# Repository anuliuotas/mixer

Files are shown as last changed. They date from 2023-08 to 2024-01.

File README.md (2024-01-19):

TODO:

### KiCad:
- MixerController: Bad mosfet footprint G and D pins are mixed up
- All: Mounting holes should be grounded
- All: Pinout should be visible at least in drawings layer

### ESPHome
- MixerController: VESC temperature sensor reading from CAN
- MixerInterface: Loading splash screen

### CAD
- Increase height of WAGO holder for more cable space

### Other
- Buy standoffs for VESC cover holder
- Check replacement parts

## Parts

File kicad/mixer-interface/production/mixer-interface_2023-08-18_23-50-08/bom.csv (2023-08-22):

Designator | Footprint | Quantity | Value | LCSC Part #
C1 | 0805 | 1 | 10u
H1, H2, H3, H4 | MountingHole_3.2mm_M3_Pad_Via | 4 | MountingHole
J1 | JST_XH_B2B-XH-AM_1x02_P2.50mm_Vertical | 1 | PWR_IN
J2 | JST_XH_B2B-XH-AM_1x02_P2.50mm_Vertical | 1 | CAN
R1, R2 | 0805 | 2 | 10k
R3, R4, R6 | 0805 | 3 | 4k7
R5 | 0805 | 1 | R120
U10 | MODULE_ESP32-DEVKITC-32U | 1 | ESP32-DEVKITC-32U
U2 | JST_XH_B5B-XH-AM_1x05_P2.50mm_Vertical | 1 | TIME_ENCODER
U3 | JST_XH_B5B-XH-AM_1x05_P2.50mm_Vertical | 1 | SPEED_ENCODER
U4 | JST_XH_B3B-XH-AM_1x03_P2.50mm_Vertical | 1 | TEMP MOTOR
U5 | JST_XH_B3B-XH-AM_1x03_P2.50mm_Vertical | 1 | TEMP MATERIAL
U6 | TJA1050 | 1 | TJA1050
U8 | display_connector_jst_xh_6 | 1 | TZT OLED312 SSD1322

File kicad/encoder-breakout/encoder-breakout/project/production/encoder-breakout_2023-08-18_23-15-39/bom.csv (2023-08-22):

Designator | Footprint | Quantity | Value | LCSC Part #
C1, C2, C3 | 0805 | 3 | C
J1 | JST_XH_S5B-XH-A_1x05_P2.50mm_Horizontal | 1 | Conn_01x05_Socket
R3, R4, R5 | 0805 | 3 | 10k
SW1 | RotaryEncoder_Alps_EC11E-Switch_Vertical_H20mm | 1 | RotaryEncoder_Switch

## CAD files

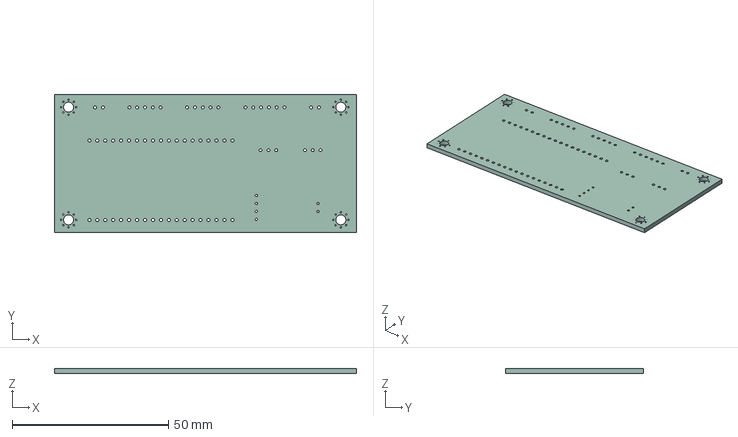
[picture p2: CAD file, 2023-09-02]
kicad/mixer-interface/mixer-interface.step
96.5 x 44.0 x 1.58 mm

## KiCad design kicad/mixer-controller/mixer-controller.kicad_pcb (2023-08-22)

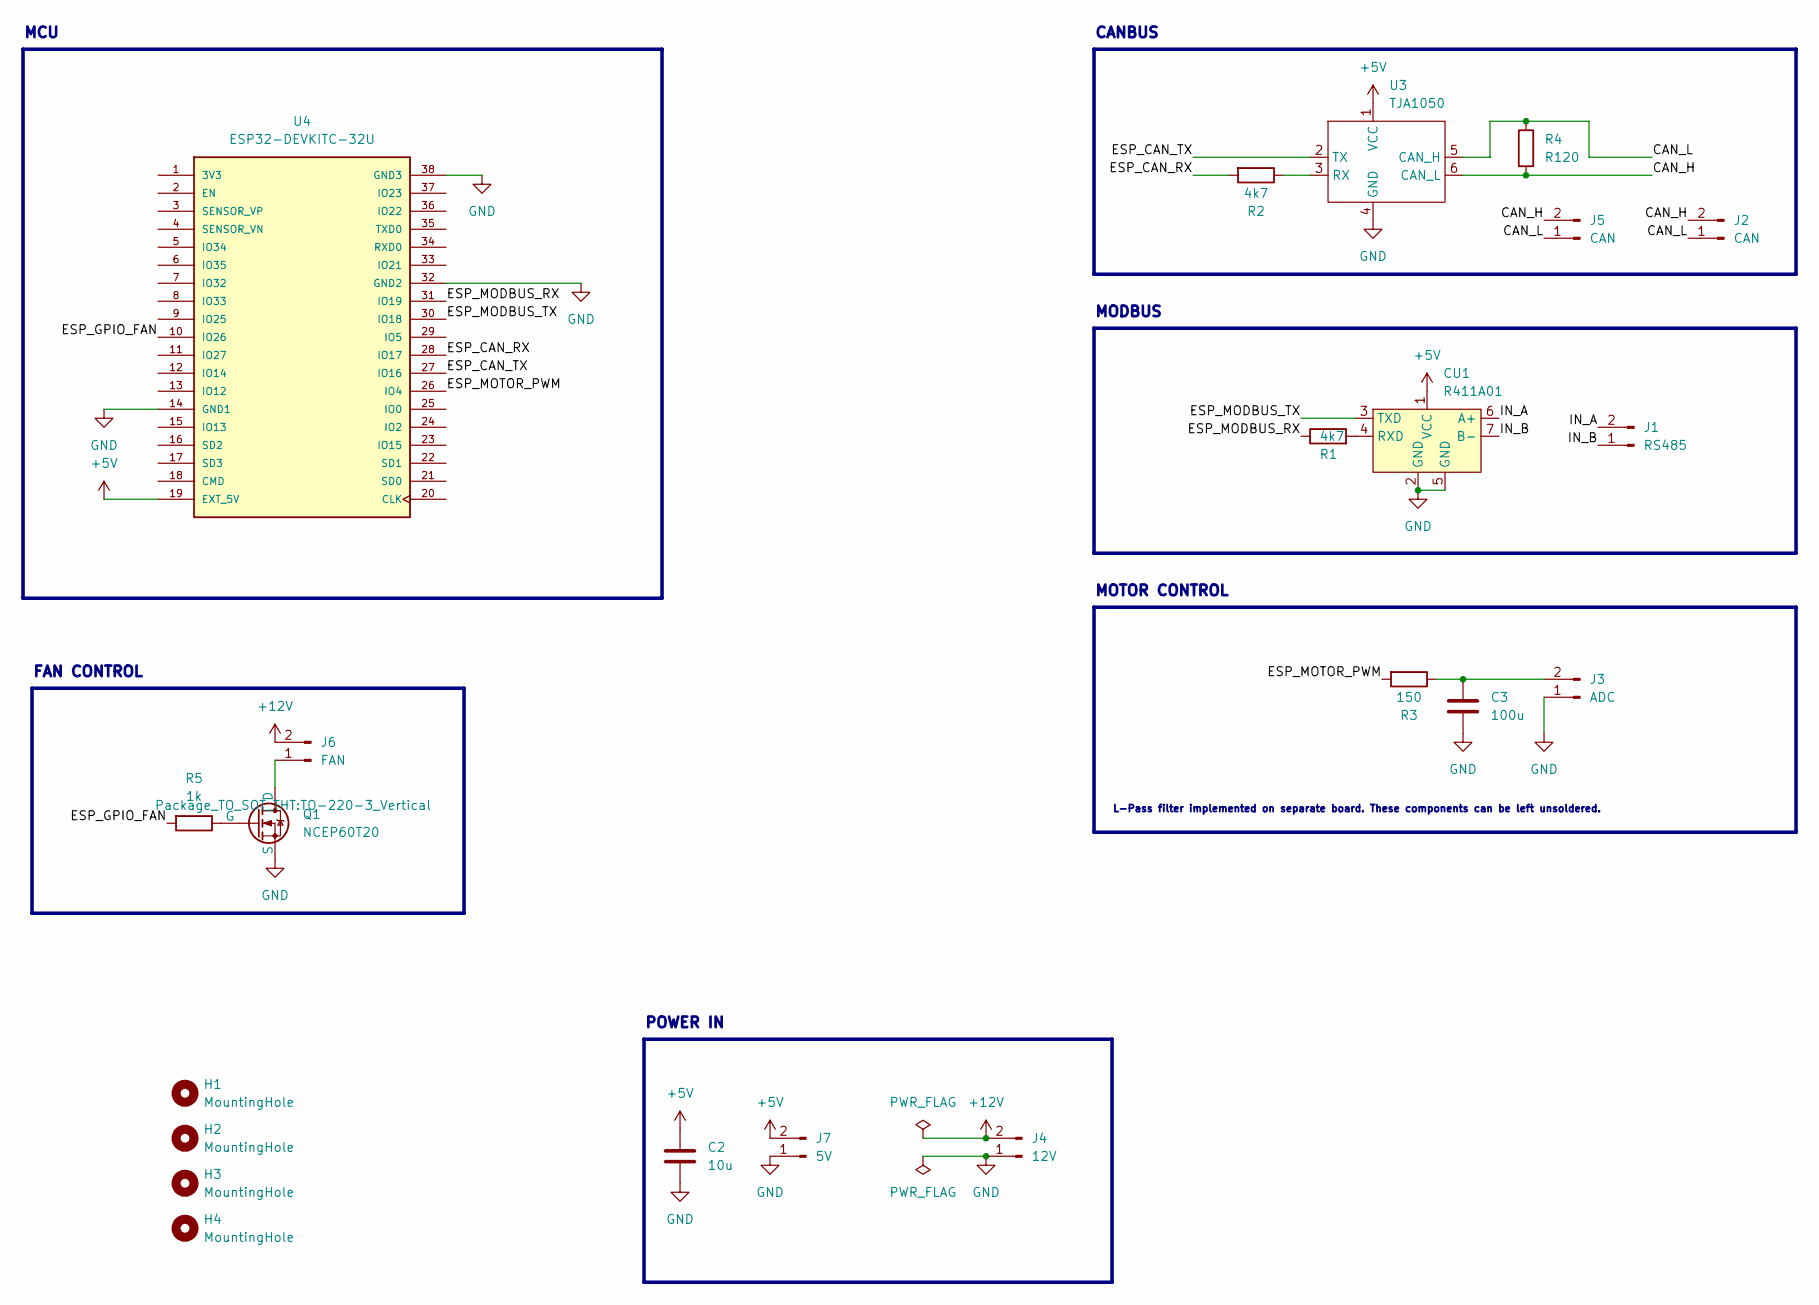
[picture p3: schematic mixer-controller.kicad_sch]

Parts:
C2: 10u; C_0805_2012Metric
C3: 100u; C_0805_2012Metric
CU1: R411A01
H1, H2, H3, H4: MountingHole; MountingHole_3.2mm_M3_Pad_Via
J1: RS485; JST_XH_B2B-XH-A_1x02_P2.50mm_Vertical
J2, J5: CAN; JST_XH_B2B-XH-A_1x02_P2.50mm_Vertical
J3: ADC; JST_XH_B2B-XH-A_1x02_P2.50mm_Vertical
J4: 12V; JST_XH_B2B-XH-A_1x02_P2.50mm_Vertical
J6: FAN; JST_XH_B2B-XH-A_1x02_P2.50mm_Vertical
J7: 5V; JST_XH_B2B-XH-A_1x02_P2.50mm_Vertical
Q1: NCEP60T20; TO-220-3_Vertical
R1: 4k7; R_0805_2012Metric
R2: 4k7; R_0805_2012Metric_Pad1.20x1.40mm_HandSolder
R3: 150; R_0805_2012Metric_Pad1.20x1.40mm_HandSolder
R4: R120; R_0805_2012Metric_Pad1.20x1.40mm_HandSolder
R5: 1k; R_0805_2012Metric_Pad1.20x1.40mm_HandSolder
U3: TJA1050
U4: ESP32-DEVKITC-32U; MODULE_ESP32-DEVKITC-32U; PARTREV N/A

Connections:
+5V: C2.1, CU1.1 (VCC), J7.2, U3.1 (VCC), U4.19 (EXT_5V)
+12V: J4.2, J6.2
/CAN_H: J2.2, J5.2, R4.2, U3.6 (CAN_L)
/CAN_L: J2.1, J5.1, R4.1, U3.5 (CAN_H)
/ESP_CAN_RX: R2.2, U4.28 (IO17)
/ESP_CAN_TX: U3.2 (TX), U4.27 (IO16)
/ESP_GPIO_FAN: R5.2, U4.10 (IO26)
/ESP_MODBUS_RX: R1.1, U4.31 (IO19)
/ESP_MODBUS_TX: CU1.3 (TXD), U4.30 (IO18)
/ESP_MOTOR_PWM: R3.2, U4.26 (IO4)
/IN_A: CU1.6 (A+), J1.2
/IN_B: CU1.7 (B-), J1.1
GND: C2.2, C3.2, CU1.2 (GND), CU1.5 (GND), J3.1, J4.1, J7.1, Q1.3 (S), U3.4 (GND), U4.14 (GND1), U4.32 (GND2), U4.38 (GND3)
unnamed: CU1.4 (RXD), R1.2
unnamed: C3.1, J3.2, R3.1
unnamed: J6.1, Q1.1 (D)
unnamed: Q1.2 (G), R5.1
unnamed: R2.1, U3.3 (RX)

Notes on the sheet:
POWER IN
FAN CONTROL
MODBUS
MCU
MOTOR CONTROL
L-Pass filter implemented on separate board. These components can be left unsoldered.
CANBUS

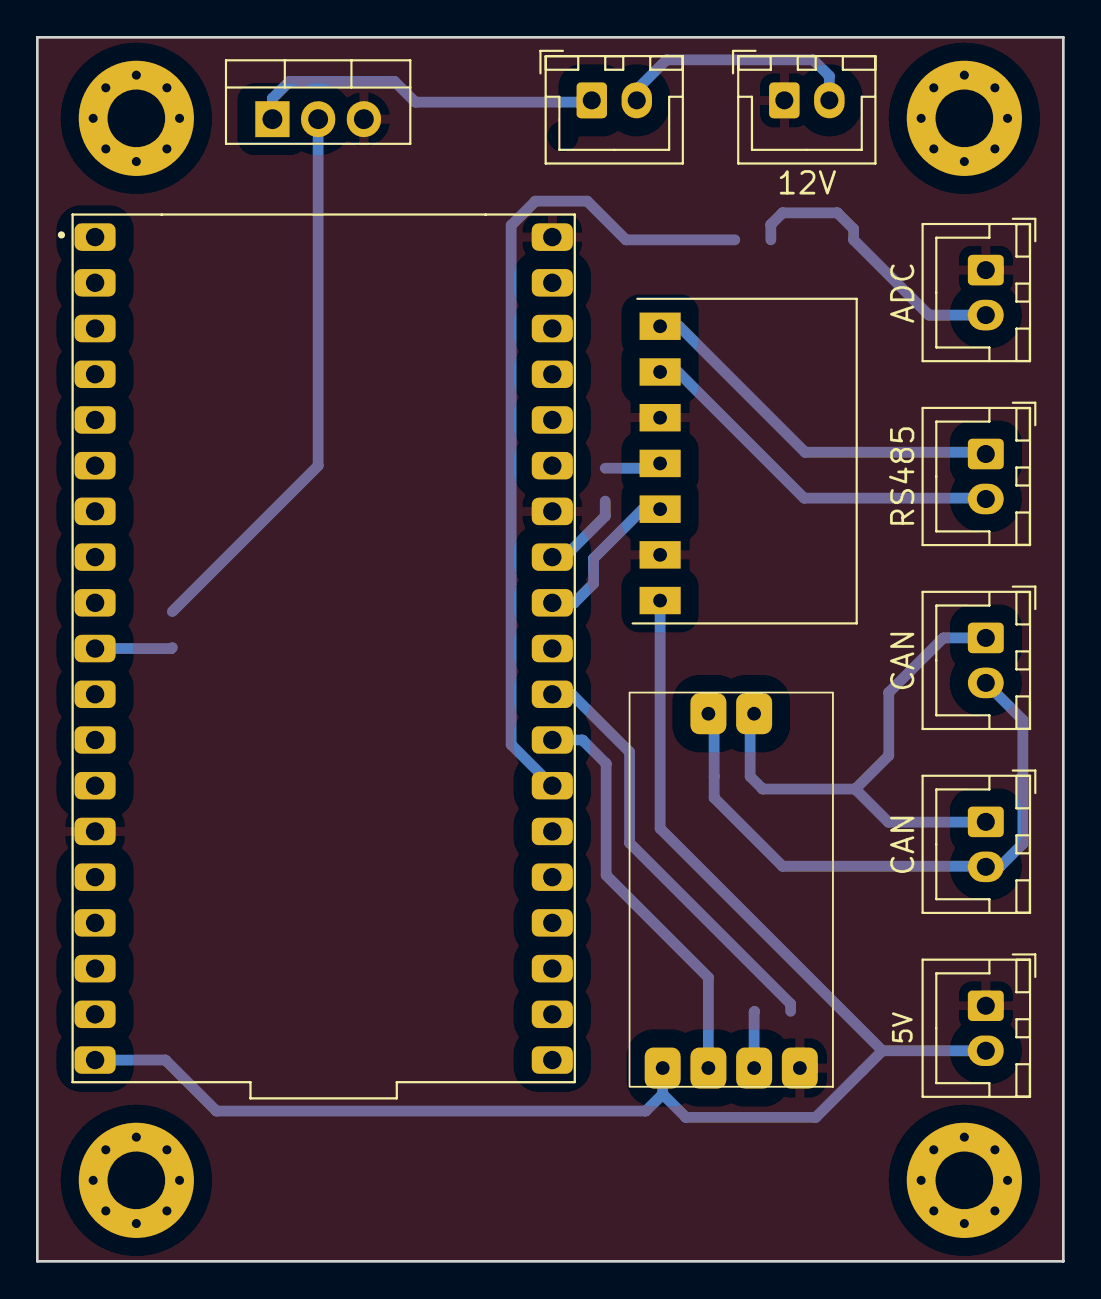
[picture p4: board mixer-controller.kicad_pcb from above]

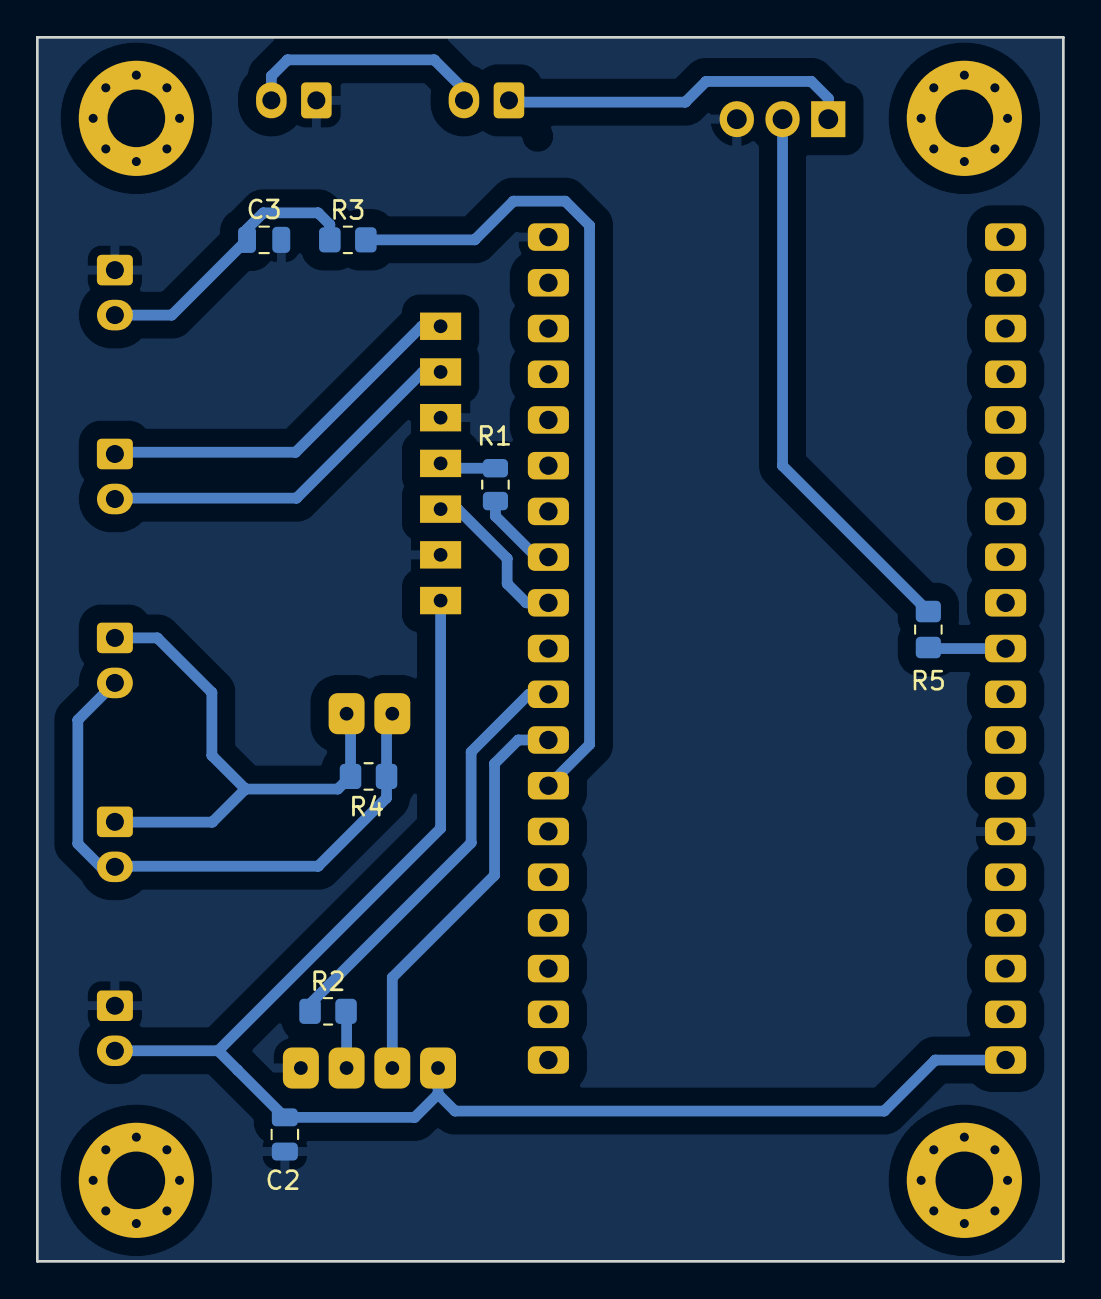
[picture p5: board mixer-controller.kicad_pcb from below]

Board: 2 copper layers, 57.0 x 68.0 mm, 22 parts (7 on the bottom side), 18 nets.

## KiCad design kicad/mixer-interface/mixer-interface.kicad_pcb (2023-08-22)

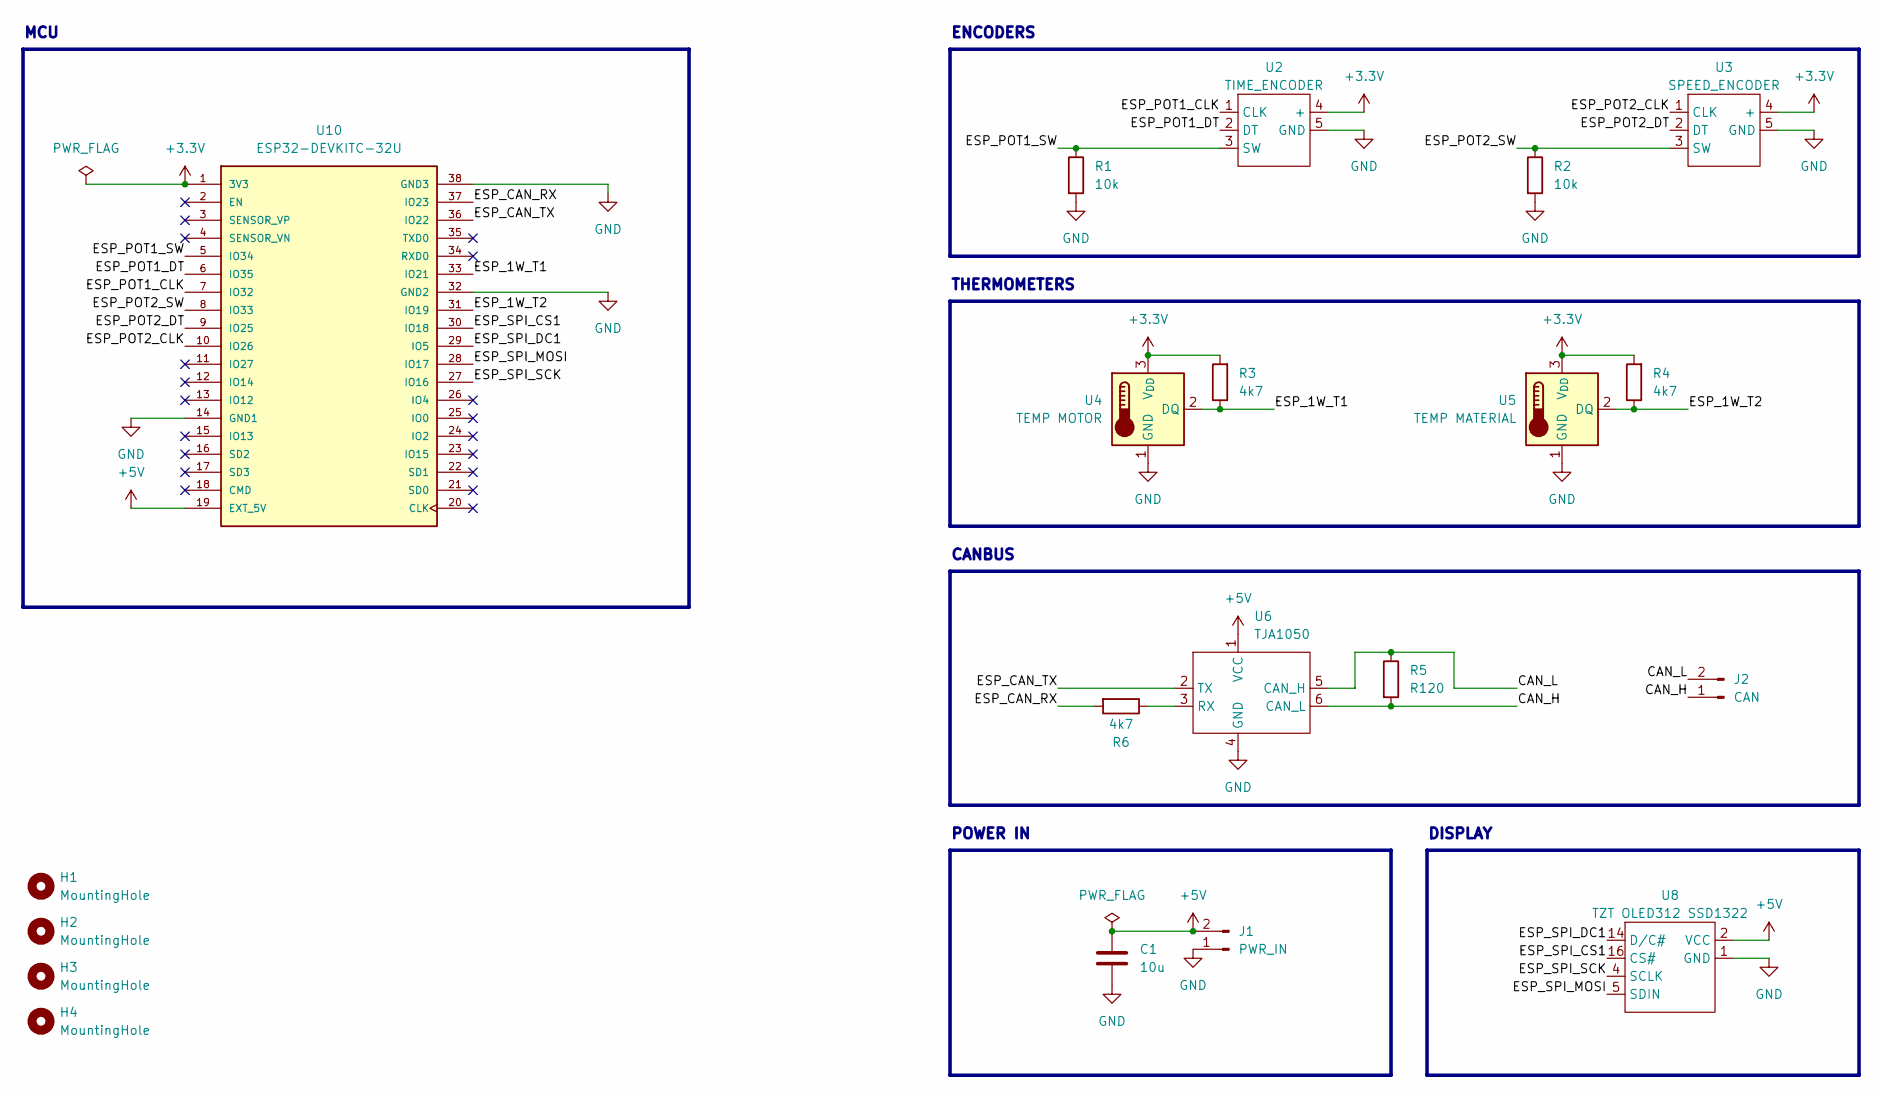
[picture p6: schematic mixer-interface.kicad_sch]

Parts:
C1: 10u; C_0805_2012Metric
H1, H2, H3, H4: MountingHole; MountingHole_3.2mm_M3_Pad_Via
J1: PWR_IN; JST_XH_B2B-XH-A_1x02_P2.50mm_Vertical
J2: CAN; JST_XH_B2B-XH-A_1x02_P2.50mm_Vertical
R1, R2: 10k; R_0805_2012Metric_Pad1.20x1.40mm_HandSolder
R3, R4, R6: 4k7; R_0805_2012Metric_Pad1.20x1.40mm_HandSolder
R5: R120; R_0805_2012Metric_Pad1.20x1.40mm_HandSolder
U2: TIME_ENCODER; JST_XH_B5B-XH-A_1x05_P2.50mm_Vertical
U3: SPEED_ENCODER; JST_XH_B5B-XH-A_1x05_P2.50mm_Vertical
U4: TEMP MOTOR; JST_XH_B3B-XH-A_1x03_P2.50mm_Vertical
U5: TEMP MATERIAL; JST_XH_B3B-XH-A_1x03_P2.50mm_Vertical
U6: TJA1050
U8: TZT OLED312 SSD1322; display_connector_jst_xh_6
U10: ESP32-DEVKITC-32U; MODULE_ESP32-DEVKITC-32U; PARTREV N/A

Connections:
+3.3V: R3.2, R4.2, U2.4 (+), U3.4 (+), U4.3 (V_{DD}), U5.3 (V_{DD}), U10.1 (3V3)
+5V: C1.1, J1.2, U6.1 (VCC), U8.2 (VCC), U10.19 (EXT_5V)
/CAN_H: J2.1, R5.2, U6.6 (CAN_L)
/CAN_L: J2.2, R5.1, U6.5 (CAN_H)
/ESP_1W_T1: R3.1, U4.2 (DQ), U10.33 (IO21)
/ESP_1W_T2: R4.1, U5.2 (DQ), U10.31 (IO19)
/ESP_CAN_RX: R6.2, U10.37 (IO23)
/ESP_CAN_TX: U6.2 (TX), U10.36 (IO22)
/ESP_POT1_CLK: U2.1 (CLK), U10.7 (IO32)
/ESP_POT1_DT: U2.2 (DT), U10.6 (IO35)
/ESP_POT1_SW: R1.1, U2.3 (SW), U10.5 (IO34)
/ESP_POT2_CLK: U3.1 (CLK), U10.10 (IO26)
/ESP_POT2_DT: U3.2 (DT), U10.9 (IO25)
/ESP_POT2_SW: R2.1, U3.3 (SW), U10.8 (IO33)
/ESP_SPI_CS1: U8.16 (CS#), U10.30 (IO18)
/ESP_SPI_DC1: U8.14 (D/C#), U10.29 (IO5)
/ESP_SPI_MOSI: U8.5 (SDIN), U10.28 (IO17)
/ESP_SPI_SCK: U8.4 (SCLK), U10.27 (IO16)
GND: C1.2, J1.1, R1.2, R2.2, U2.5 (GND), U3.5 (GND), U4.1 (GND), U5.1 (GND), U6.4 (GND), U8.1 (GND), U10.14 (GND1), U10.32 (GND2), U10.38 (GND3)
unnamed: R6.1, U6.3 (RX)

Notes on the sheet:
CANBUS
DISPLAY
MCU
POWER IN
THERMOMETERS
ENCODERS

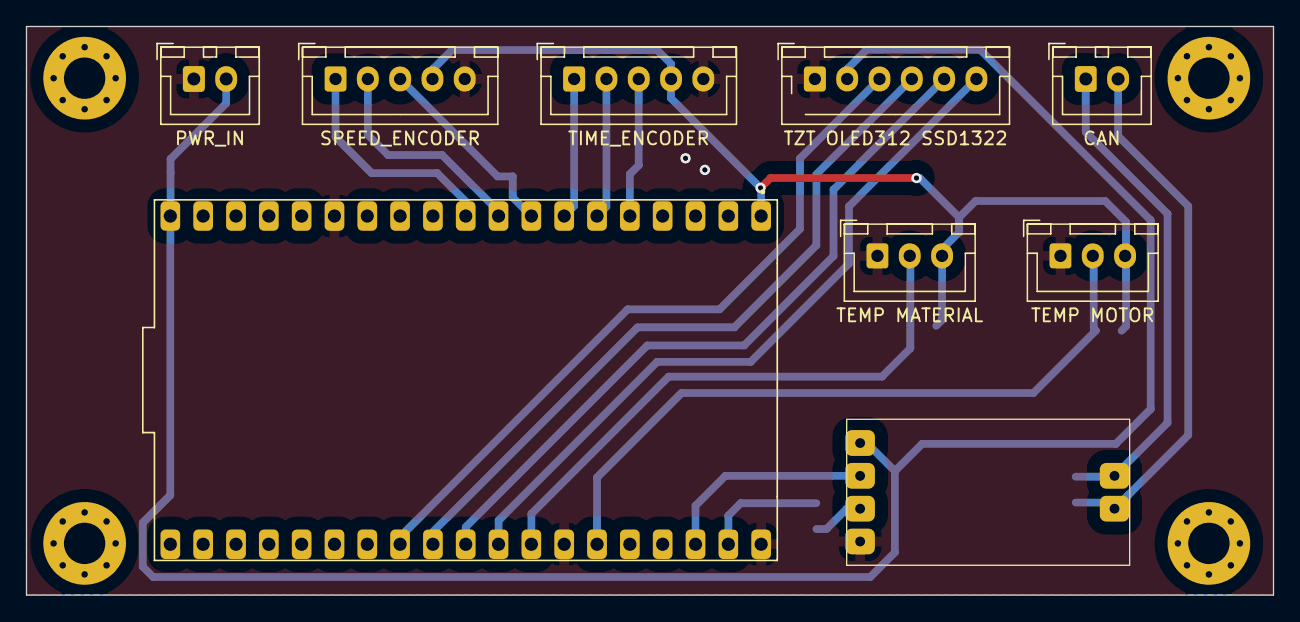
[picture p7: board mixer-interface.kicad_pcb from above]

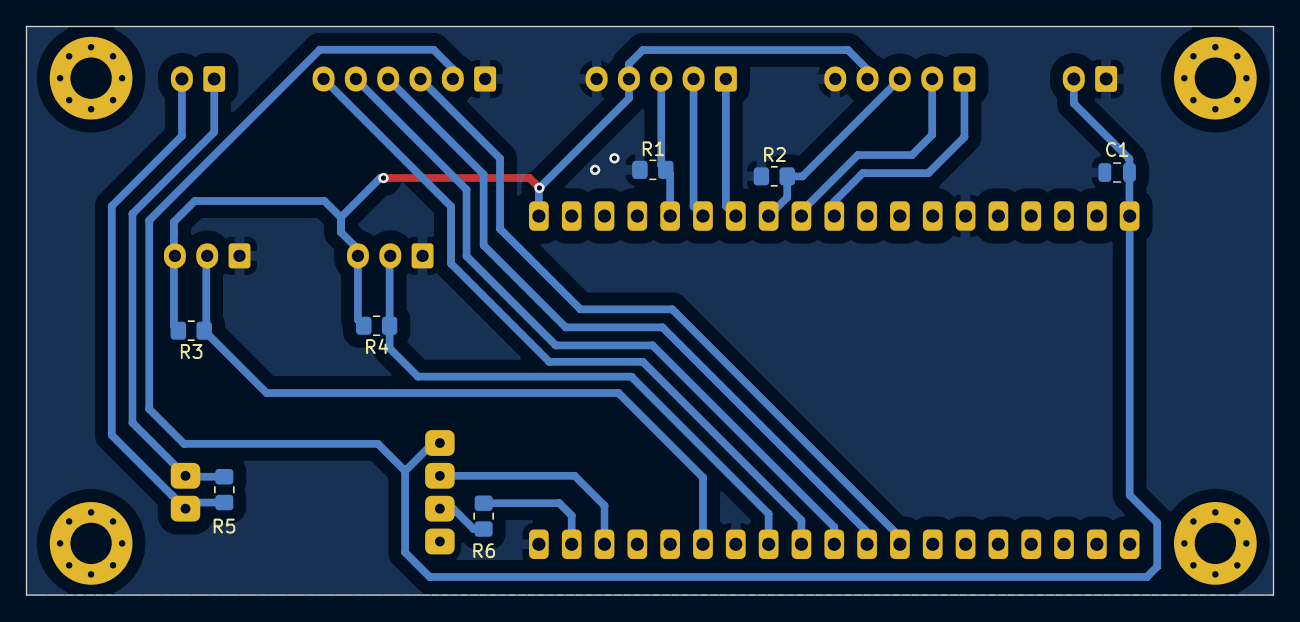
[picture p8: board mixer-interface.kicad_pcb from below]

Board: 2 copper layers, 96.5 x 44.0 mm, 20 parts (7 on the bottom side), 20 nets.

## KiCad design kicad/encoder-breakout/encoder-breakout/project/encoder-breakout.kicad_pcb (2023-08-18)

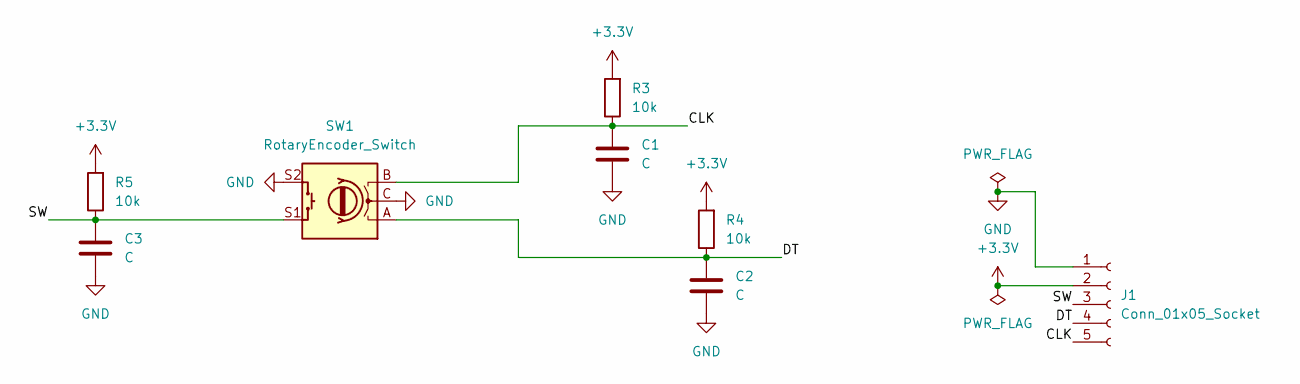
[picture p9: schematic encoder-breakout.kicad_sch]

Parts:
C1, C2, C3: C; C_0805_2012Metric_Pad1.18x1.45mm_HandSolder
J1: Conn_01x05_Socket; JST_XH_S5B-XH-A_1x05_P2.50mm_Horizontal
R3, R4, R5: 10k; R_0805_2012Metric_Pad1.20x1.40mm_HandSolder
SW1: RotaryEncoder_Switch; RotaryEncoder_Alps_EC11E-Switch_Vertical_H20mm

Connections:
+3.3V: J1.2, R3.2, R4.2, R5.2
/CLK: C1.1, J1.5, R3.1, SW1.B
/DT: C2.1, J1.4, R4.1, SW1.A
/SW: C3.1, J1.3, R5.1, SW1.S1
GND: C1.2, C2.2, C3.2, J1.1, SW1.C, SW1.S2

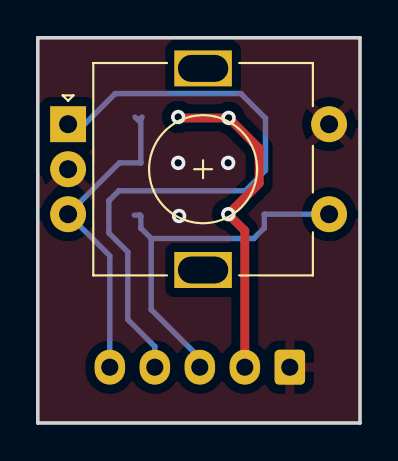
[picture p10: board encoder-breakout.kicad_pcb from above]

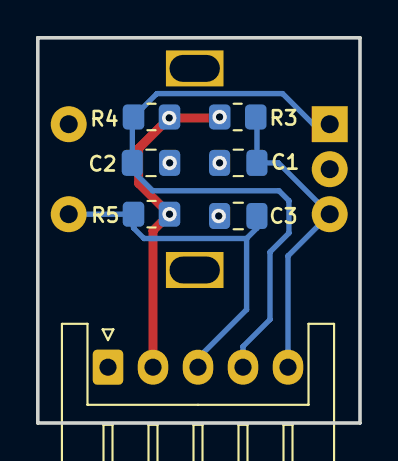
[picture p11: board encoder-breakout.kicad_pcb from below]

Board: 2 copper layers, 17.9 x 21.4 mm, 8 parts (7 on the bottom side), 5 nets.

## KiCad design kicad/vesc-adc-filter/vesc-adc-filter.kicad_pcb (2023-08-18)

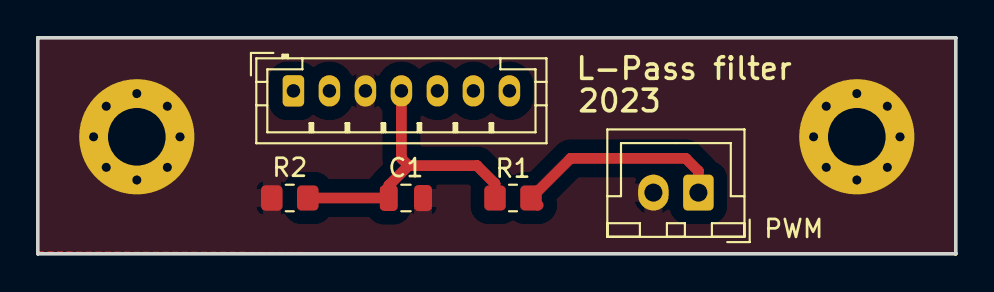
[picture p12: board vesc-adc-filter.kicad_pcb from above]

Board: 2 copper layers, 51.0 x 12.0 mm, 7 parts (0 on the bottom side), 3 nets.

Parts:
C1: 100u; C_0805_2012Metric
H1, H2: MountingHole; MountingHole_3.2mm_M3_Pad_Via
J1: PWM; JST_XH_B2B-XH-A_1x02_P2.50mm_Vertical
R1: 150; R_0805_2012Metric_Pad1.20x1.40mm_HandSolder
R2: 100k; R_0805_2012Metric_Pad1.20x1.40mm_HandSolder
U1: JST_PH_B7B-PH-K_1x07_P2.00mm_Vertical

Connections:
GND: C1.2, J1.2, R2.2, U1.3 (GND)
unnamed: J1.1, R1.2
unnamed: C1.1, R1.1, R2.1, U1.4 (ADC1)

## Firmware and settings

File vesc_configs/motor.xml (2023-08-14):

<?xml version="1.0" encoding="UTF-8"?>
<MCConfiguration>
    <pwm_mode>1</pwm_mode>
    <comm_mode>0</comm_mode>
    <motor_type>2</motor_type>
    <sensor_mode>0</sensor_mode>
    <l_current_max>15</l_current_max>
    <l_current_min>0</l_current_min>
    <l_in_current_max>15</l_in_current_max>
    <l_in_current_min>0</l_in_current_min>
    <l_abs_current_max>18</l_abs_current_max>
    <l_min_erpm>-100000</l_min_erpm>
    <l_max_erpm>100000</l_max_erpm>
    <l_erpm_start>0.8</l_erpm_start>
    <l_max_erpm_fbrake>300</l_max_erpm_fbrake>
    <l_max_erpm_fbrake_cc>1500</l_max_erpm_fbrake_cc>
    <l_min_vin>8</l_min_vin>
    <l_max_vin>57</l_max_vin>
    <l_battery_cut_start>10</l_battery_cut_start>
    <l_battery_cut_end>8</l_battery_cut_end>
    <l_slow_abs_current>1</l_slow_abs_current>
    <l_temp_fet_start>60</l_temp_fet_start>
    <l_temp_fet_end>70</l_temp_fet_end>
    <l_temp_motor_start>85</l_temp_motor_start>
    <l_temp_motor_end>100</l_temp_motor_end>
    <l_temp_accel_dec>0.15</l_temp_accel_dec>
    <l_min_duty>0</l_min_duty>
    <l_max_duty>0.95</l_max_duty>
    <l_watt_max>1.5e+06</l_watt_max>
    <l_watt_min>-1.5e+06</l_watt_min>
    <l_current_max_scale>1</l_current_max_scale>
    <l_current_min_scale>1</l_current_min_scale>
    <l_duty_start>1</l_duty_start>
    <sl_min_erpm>150</sl_min_erpm>
    <sl_min_erpm_cycle_int_limit>1100</sl_min_erpm_cycle_int_limit>
    <sl_max_fullbreak_current_dir_change>10</sl_max_fullbreak_current_dir_change>
    <sl_cycle_int_limit>62</sl_cycle_int_limit>
    <sl_phase_advance_at_br>0.8</sl_phase_advance_at_br>
    <sl_cycle_int_rpm_br>80000</sl_cycle_int_rpm_br>
    <sl_bemf_coupling_k>600</sl_bemf_coupling_k>
    <hall_table__0>-1</hall_table__0>
    <hall_table__1>1</hall_table__1>
    <hall_table__2>3</hall_table__2>
    <hall_table__3>2</hall_table__3>
    <hall_table__4>5</hall_table__4>
    <hall_table__5>6</hall_table__5>
    <hall_table__6>4</hall_table__6>
    <hall_table__7>-1</hall_table__7>
    <hall_sl_erpm>2000</hall_sl_erpm>
    <foc_current_kp>0.0044</foc_current_kp>
    <foc_current_ki>33.17</foc_current_ki>
    <foc_f_sw>40000</foc_f_sw>
    <foc_dt_us>0.12</foc_dt_us>
    <foc_encoder_inverted>0</foc_encoder_inverted>
    <foc_encoder_offset>180</foc_encoder_offset>
    <foc_encoder_ratio>7</foc_encoder_ratio>
    <foc_encoder_sin_gain>1</foc_encoder_sin_gain>
    <foc_encoder_cos_gain>1</foc_encoder_cos_gain>
    <foc_encoder_sin_offset>1.65</foc_encoder_sin_offset>
    <foc_encoder_cos_offset>1.65</foc_encoder_cos_offset>
    <foc_encoder_sincos_filter_constant>0.5</foc_encoder_sincos_filter_constant>
    <foc_sensor_mode>0</foc_sensor_mode>
    <foc_pll_kp>2000</foc_pll_kp>
    <foc_pll_ki>30000</foc_pll_ki>
    <foc_motor_l>4.45e-06</foc_motor_l>
    <foc_motor_r>0.0332</foc_motor_r>
    <foc_motor_flux_linkage>0.002464</foc_motor_flux_linkage>
    <foc_observer_gain>1.6471e+08</foc_observer_gain>
    <foc_observer_gain_slow>0.05</foc_observer_gain_slow>
    <foc_duty_dowmramp_kp>10</foc_duty_dowmramp_kp>
    <foc_duty_dowmramp_ki>200</foc_duty_dowmramp_ki>
    <foc_openloop_rpm>400</foc_openloop_rpm>
    <foc_sl_openloop_hyst>0.1</foc_sl_openloop_hyst>
    <foc_sl_openloop_time>0.1</foc_sl_openloop_time>
    <foc_sl_d_current_duty>0</foc_sl_d_current_duty>
    <foc_sl_d_current_factor>0</foc_sl_d_current_factor>
    <foc_hall_table__0>255</foc_hall_table__0>
    <foc_hall_table__1>255</foc_hall_table__1>
    <foc_hall_table__2>255</foc_hall_table__2>
    <foc_hall_table__3>255</foc_hall_table__3>
    <foc_hall_table__4>255</foc_hall_table__4>
    <foc_hall_table__5>255</foc_hall_table__5>
    <foc_hall_table__6>255</foc_hall_table__6>
    <foc_hall_table__7>255</foc_hall_table__7>
    <foc_sl_erpm>2500</foc_sl_erpm>
    <foc_sample_v0_v7>0</foc_sample_v0_v7>
    <foc_sample_high_current>0</foc_sample_high_current>
    <foc_sat_comp>0</foc_sat_comp>
    <foc_temp_comp>0</foc_temp_comp>
    <foc_temp_comp_base_temp>25</foc_temp_comp_base_temp>
    <foc_current_filter_const>0.1</foc_current_filter_const>
    <foc_cc_decoupling>2</foc_cc_decoupling>
    <foc_observer_type>0</foc_observer_type>
    <foc_hfi_voltage_start>20</foc_hfi_voltage_start>
    <foc_hfi_voltage_run>4</foc_hfi_voltage_run>
    <foc_hfi_voltage_max>10</foc_hfi_voltage_max>
    <foc_sl_erpm_hfi>2000</foc_sl_erpm_hfi>
    <foc_hfi_start_samples>65</foc_hfi_start_samples>
    <foc_hfi_obs_ovr_sec>0.001</foc_hfi_obs_ovr_sec>
    <foc_hfi_samples>1</foc_hfi_samples>
    <gpd_buffer_notify_left>200</gpd_buffer_notify_left>
    <gpd_buffer_interpol>0</gpd_buffer_interpol>
    <gpd_current_filter_const>0.1</gpd_current_filter_const>
    <gpd_current_kp>0.03</gpd_current_kp>
    <gpd_current_ki>50</gpd_current_ki>
    <s_pid_kp>0.004</s_pid_kp>
    <s_pid_ki>0.004</s_pid_ki>
    <s_pid_kd>0.0001</s_pid_kd>
    <s_pid_kd_filter>0.2</s_pid_kd_filter>
    <s_pid_min_erpm>900</s_pid_min_erpm>
    <s_pid_allow_braking>1</s_pid_allow_braking>
    <p_pid_kp>0.03</p_pid_kp>
    <p_pid_ki>0</p_pid_ki>
    <p_pid_kd>0.0004</p_pid_kd>
    <p_pid_kd_filter>0.2</p_pid_kd_filter>
    <p_pid_ang_div>1</p_pid_ang_div>
    <cc_startup_boost_duty>0.01</cc_startup_boost_duty>
    <cc_min_current>0.05</cc_min_current>
    <cc_gain>0.0046</cc_gain>
    <cc_ramp_step_max>0.04</cc_ramp_step_max>
    <m_fault_stop_time_ms>500</m_fault_stop_time_ms>
    <m_duty_ramp_step>0.02</m_duty_ramp_step>
    <m_current_backoff_gain>0.5</m_current_backoff_gain>
    <m_encoder_counts>8192</m_encoder_counts>
    <m_sensor_port_mode>0</m_sensor_port_mode>
    <m_invert_direction>1</m_invert_direction>
    <m_drv8301_oc_mode>3</m_drv8301_oc_mode>
    <m_drv8301_oc_adj>25</m_drv8301_oc_adj>
    <m_bldc_f_sw_min>3000</m_bldc_f_sw_min>
    <m_bldc_f_sw_max>35000</m_bldc_f_sw_max>
    <m_dc_f_sw>25000</m_dc_f_sw>
    <m_ntc_motor_beta>3380</m_ntc_motor_beta>
    <m_out_aux_mode>0</m_out_aux_mode>
    <m_motor_temp_sens_type>0</m_motor_temp_sens_type>
    <m_ptc_motor_coeff>0.61</m_ptc_motor_coeff>
    <si_motor_poles>14</si_motor_poles>
    <si_gear_ratio>3</si_gear_ratio>
    <si_wheel_diameter>0.083</si_wheel_diameter>
    <si_battery_type>0</si_battery_type>
    <si_battery_cells>3</si_battery_cells>
    <si_battery_ah>6</si_battery_ah>
    <motor_brand>Unnamed</motor_brand>
    <motor_model>Not Specified</motor_model>
    <motor_weight>0</motor_weight>
    <motor_poles>14</motor_poles>
    <motor_sensor_type>0</motor_sensor_type>
    <motor_description>&lt;!DOCTYPE HTML PUBLIC &quot;-//W3C//DTD HTML 4.0//EN&quot; &quot;http://www.w3.org/TR/REC-html40/strict.dtd&quot;&gt;
&lt;html&gt;&lt;head&gt;&lt;meta name=&quot;qrichtext&quot; content=&quot;1&quot; /&gt;&lt;style type=&quot;text/css&quot;&gt;
p, li { white-space: pre-wrap; }
&lt;/style&gt;&lt;/head&gt;&lt;body style=&quot; font-family:'Roboto'; font-size:12pt; font-weight:400; font-style:normal;&quot;&gt;
&lt;p style=&quot; margin-top:0px; margin-bottom:0px; margin-left:0px; margin-right:0px; -qt-block-indent:0; text-indent:0px;&quot;&gt;A motor description can be edited here.&lt;/p&gt;&lt;/body&gt;&lt;/html&gt;</motor_description>
    <motor_loss_torque>0.03</motor_loss_torque>
    <motor_quality_bearings>0</motor_quality_bearings>
    <motor_quality_magnets>0</motor_quality_magnets>
    <motor_quality_construction>0</motor_quality_construction>
    <motor_quality_description>&lt;!DOCTYPE HTML PUBLIC &quot;-//W3C//DTD HTML 4.0//EN&quot; &quot;http://www.w3.org/TR/REC-html40/strict.dtd&quot;&gt;
&lt;html&gt;&lt;head&gt;&lt;meta name=&quot;qrichtext&quot; content=&quot;1&quot; /&gt;&lt;style type=&quot;text/css&quot;&gt;
p, li { white-space: pre-wrap; }
&lt;/style&gt;&lt;/head&gt;&lt;body style=&quot; font-family:'Roboto'; font-size:12pt; font-weight:400; font-style:normal;&quot;&gt;
&lt;p style=&quot; margin-top:0px; margin-bottom:0px; margin-left:0px; margin-right:0px; -qt-block-indent:0; text-indent:0px;&quot;&gt;Some comments about the motor quality. Images can be added as well.&lt;/p&gt;&lt;/body&gt;&lt;/html&gt;</motor_quality_description>
</MCConfiguration>

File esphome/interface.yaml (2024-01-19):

substitutions:
  device_name: "mixer-test"
  device_friendly_name: "Mixer test"
  mqqt_root_topic: "device"
  mqqt_retain_message: "false"

esphome:
  name: ${device_name}
  friendly_name: ${device_friendly_name}

esp32:
  board: nodemcu-32s

logger:
  level: INFO
  baud_rate: 9600
  logs:
    canbus: INFO

dallas:
  - pin: GPIO19
    id: hub_1
    update_interval: 5s
  - pin: GPIO21
    id: hub_2
    update_interval: 5s

sensor:
  - platform: dallas
    dallas_id: hub_1
    id: temp_motor
    index: 0

  - platform: dallas
    dallas_id: hub_2
    id: temp_material
    index: 0

  - platform: rotary_encoder
    id: time_encoder
    name: "Time encoder"
    pin_a: GPIO25
    pin_b: GPIO26
    min_value: 0
    max_value: 6000
    restore_mode: ALWAYS_ZERO
    resolution: 2
    filters:
      - multiply: 5
      - lambda: |-
          // If timer is ON, encoder value change is not allowed
          if (id(timer_state).state) {
            return {};
          }
          return x;
  
  - platform: rotary_encoder
    id: speed_encoder
    name: "Speed encoder"
    pin_a: GPIO35
    pin_b: GPIO32
    min_value: 0
    max_value: 100
    restore_mode: ALWAYS_ZERO
    resolution: 2
    filters:
      - multiply: 1

binary_sensor:
  - platform: gpio
    id: time_encoder_sw
    pin:
      number: GPIO33
      inverted: true
    on_press:
      then:
        - switch.toggle: timer_state
    
  - platform: gpio
    id: speed_encoder_sw
    pin:
      number: GPIO34
      inverted: true
    on_press:
      then:
        - switch.toggle: motor_state

switch:
  - platform: template
    id: motor_state
    optimistic: true
    restore_mode: ALWAYS_OFF
  - platform: template
    id: timer_state
    optimistic: true
    restore_mode: ALWAYS_OFF
    turn_on_action:
      - lambda: |-
          id(timer_update_ms) = 0;


globals:
  - id: timer_counter_ms
    type: long
    initial_value: '0'
    restore_value: no
  - id: timer_update_ms
    type: long
    initial_value: '0'
    restore_value: no
  - id: text_blink
    type: bool
    restore_value: no
  - id: speed_esp_rpm
    type: float
    initial_value: '0'
    restore_value: no

interval:
  # - interval: 250ms
  #   then:
  #       - lambda: |-
  #           // Text blink interval
  #           id(text_blink) = !id(text_blink);

  - interval: 100ms
    then:
      - lambda: |-
          // Udate timer
          if (id(timer_state).state) {
            
            // Update timer counter
            long current_millis = millis();
            long previous_timer_update_ms = id(timer_update_ms);

            if (previous_timer_update_ms == 0) {
              id(timer_update_ms) = current_millis;
              return;
            }

            long delta_millis = current_millis - previous_timer_update_ms;
            long updated_value = id(timer_counter_ms) + delta_millis;

            id(timer_counter_ms) = updated_value;
            id(timer_update_ms) = current_millis;

            if (float(updated_value) / 1000 > id(time_encoder).state) {
              // Timer has reach the setpoint
              id(timer_state).turn_off();
              id(motor_state).turn_off();

              id(timer_counter_ms) = 0;
              id(timer_update_ms) = 0;
            }
          } 
          
  - interval: 500ms
    then:
      - lambda: |-
          //if (millis() < 0) {
          //  return;
          //}
          // Send CAN bus message updating the speed setpoint

          int setpoint_req = 0;
          if (id(motor_state).state) {
            if (!isnan(id(speed_encoder).state)) {
              int speed_encoder_value = int(id(speed_encoder).state);
              if (speed_encoder_value > 0) {
                setpoint_req = int(speed_encoder_value);
              } 
            }
          }

          float value = float(setpoint_req);
          std::vector<uint8_t> bytes(sizeof(float));
          std::memcpy(&bytes[0], &value, sizeof(float));
          id(my_mcp2515)->send_data(1, true, bytes);
  - interval: 1000ms
    then:
      - lambda: |-
          // Send CAN bus messages updating the states
          if (millis() < 0) {
            return;
          }
          std::vector<uint8_t> bytes(sizeof(float));
          
          if (!isnan(id(temp_motor).state)) {
            std::memcpy(&bytes[0], &id(temp_motor).state, sizeof(float));
            id(my_mcp2515)->send_data(10, true, bytes);
          }

          if (!isnan(id(temp_motor).state)) {
            std::memcpy(&bytes[0], &id(temp_material).state, sizeof(float));
            id(my_mcp2515)->send_data(11, true, bytes);
          }
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

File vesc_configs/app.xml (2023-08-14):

<?xml version="1.0" encoding="UTF-8"?>
<APPConfiguration>
    <ConfigVersion>2</ConfigVersion>
    <controller_id>1</controller_id>
    <timeout_msec>1000</timeout_msec>
    <timeout_brake_current>0</timeout_brake_current>
    <send_can_status>5</send_can_status>
    <send_can_status_rate_hz>5</send_can_status_rate_hz>
    <can_baud_rate>0</can_baud_rate>
    <pairing_done>0</pairing_done>
    <permanent_uart_enabled>1</permanent_uart_enabled>
    <shutdown_mode>7</shutdown_mode>
    <can_mode>0</can_mode>
    <uavcan_esc_index>0</uavcan_esc_index>
    <app_to_use>2</app_to_use>
    <app_ppm_conf.ctrl_type>0</app_ppm_conf.ctrl_type>
    <app_ppm_conf.pid_max_erpm>15000</app_ppm_conf.pid_max_erpm>
    <app_ppm_conf.hyst>0.15</app_ppm_conf.hyst>
    <app_ppm_conf.pulse_start>1</app_ppm_conf.pulse_start>
    <app_ppm_conf.pulse_end>2</app_ppm_conf.pulse_end>
    <app_ppm_conf.pulse_center>1.5</app_ppm_conf.pulse_center>
    <app_ppm_conf.median_filter>1</app_ppm_conf.median_filter>
    <app_ppm_conf.safe_start>1</app_ppm_conf.safe_start>
    <app_ppm_conf.throttle_exp>0</app_ppm_conf.throttle_exp>
    <app_ppm_conf.throttle_exp_brake>0</app_ppm_conf.throttle_exp_brake>
    <app_ppm_conf.throttle_exp_mode>2</app_ppm_conf.throttle_exp_mode>
    <app_ppm_conf.ramp_time_pos>0.4</app_ppm_conf.ramp_time_pos>
    <app_ppm_conf.ramp_time_neg>0.2</app_ppm_conf.ramp_time_neg>
    <app_ppm_conf.multi_esc>1</app_ppm_conf.multi_esc>
    <app_ppm_conf.tc>0</app_ppm_conf.tc>
    <app_ppm_conf.tc_max_diff>3000</app_ppm_conf.tc_max_diff>
    <app_ppm_conf.max_erpm_for_dir>4000</app_ppm_conf.max_erpm_for_dir>
    <app_ppm_conf.smart_rev_max_duty>0.07</app_ppm_conf.smart_rev_max_duty>
    <app_ppm_conf.smart_rev_ramp_time>3</app_ppm_conf.smart_rev_ramp_time>
    <app_adc_conf.ctrl_type>9</app_adc_conf.ctrl_type>
    <app_adc_conf.hyst>0.01</app_adc_conf.hyst>
    <app_adc_conf.voltage_start>0.15</app_adc_conf.voltage_start>
    <app_adc_conf.voltage_end>3.25</app_adc_conf.voltage_end>
    <app_adc_conf.voltage_center>2</app_adc_conf.voltage_center>
    <app_adc_conf.voltage2_start>0.9</app_adc_conf.voltage2_start>
    <app_adc_conf.voltage2_end>3</app_adc_conf.voltage2_end>
    <app_adc_conf.use_filter>1</app_adc_conf.use_filter>
    <app_adc_conf.safe_start>1</app_adc_conf.safe_start>
    <app_adc_conf.cc_button_inverted>0</app_adc_conf.cc_button_inverted>
    <app_adc_conf.rev_button_inverted>0</app_adc_conf.rev_button_inverted>
    <app_adc_conf.voltage_inverted>0</app_adc_conf.voltage_inverted>
    <app_adc_conf.voltage2_inverted>0</app_adc_conf.voltage2_inverted>
    <app_adc_conf.throttle_exp>0</app_adc_conf.throttle_exp>
    <app_adc_conf.throttle_exp_brake>0</app_adc_conf.throttle_exp_brake>
    <app_adc_conf.throttle_exp_mode>2</app_adc_conf.throttle_exp_mode>
    <app_adc_conf.ramp_time_pos>10</app_adc_conf.ramp_time_pos>
    <app_adc_conf.ramp_time_neg>2</app_adc_conf.ramp_time_neg>
    <app_adc_conf.multi_esc>1</app_adc_conf.multi_esc>
    <app_adc_conf.tc>0</app_adc_conf.tc>
    <app_adc_conf.tc_max_diff>3000</app_adc_conf.tc_max_diff>
    <app_adc_conf.update_rate_hz>1000</app_adc_conf.update_rate_hz>
    <app_uart_baudrate>115200</app_uart_baudrate>
    <app_chuk_conf.ctrl_type>1</app_chuk_conf.ctrl_type>
    <app_chuk_conf.hyst>0.15</app_chuk_conf.hyst>
    <app_chuk_conf.ramp_time_pos>0.4</app_chuk_conf.ramp_time_pos>
    <app_chuk_conf.ramp_time_neg>0.2</app_chuk_conf.ramp_time_neg>
    <app_chuk_conf.stick_erpm_per_s_in_cc>3000</app_chuk_conf.stick_erpm_per_s_in_cc>
    <app_chuk_conf.throttle_exp>0</app_chuk_conf.throttle_exp>
    <app_chuk_conf.throttle_exp_brake>0</app_chuk_conf.throttle_exp_brake>
    <app_chuk_conf.throttle_exp_mode>2</app_chuk_conf.throttle_exp_mode>
    <app_chuk_conf.multi_esc>1</app_chuk_conf.multi_esc>
    <app_chuk_conf.tc>0</app_chuk_conf.tc>
    <app_chuk_conf.tc_max_diff>3000</app_chuk_conf.tc_max_diff>
    <app_chuk_conf.use_smart_rev>1</app_chuk_conf.use_smart_rev>
    <app_chuk_conf.smart_rev_max_duty>0.07</app_chuk_conf.smart_rev_max_duty>
    <app_chuk_conf.smart_rev_ramp_time>3</app_chuk_conf.smart_rev_ramp_time>
    <app_nrf_conf.speed>1</app_nrf_conf.speed>
    <app_nrf_conf.power>3</app_nrf_conf.power>
    <app_nrf_conf.crc_type>1</app_nrf_conf.crc_type>
    <app_nrf_conf.retry_delay>0</app_nrf_conf.retry_delay>
    <app_nrf_conf.retries>3</app_nrf_conf.retries>
    <app_nrf_conf.channel>76</app_nrf_conf.channel>
    <app_nrf_conf.address__0>198</app_nrf_conf.address__0>
    <app_nrf_conf.address__1>199</app_nrf_conf.address__1>
    <app_nrf_conf.address__2>0</app_nrf_conf.address__2>
    <app_nrf_conf.send_crc_ack>1</app_nrf_conf.send_crc_ack>
    <app_balance_conf.kp>0</app_balance_conf.kp>
    <app_balance_conf.ki>0</app_balance_conf.ki>
    <app_balance_conf.kd>0</app_balance_conf.kd>
    <app_balance_conf.hertz>1000</app_balance_conf.hertz>
    <app_balance_conf.pitch_fault>20</app_balance_conf.pitch_fault>
    <app_balance_conf.roll_fault>45</app_balance_conf.roll_fault>
    <app_balance_conf.adc1>0</app_balance_conf.adc1>
    <app_balance_conf.adc2>0</app_balance_conf.adc2>
    <app_balance_conf.overspeed_duty>0.9</app_balance_conf.overspeed_duty>
    <app_balance_conf.tiltback_duty>0.75</app_balance_conf.tiltback_duty>
    <app_balance_conf.tiltback_angle>15</app_balance_conf.tiltback_angle>
    <app_balance_conf.tiltback_speed>5</app_balance_conf.tiltback_speed>
    <app_balance_conf.tiltback_high_voltage>100</app_balance_conf.tiltback_high_voltage>
    <app_balance_conf.tiltback_low_voltage>0</app_balance_conf.tiltback_low_voltage>
    <app_balance_conf.startup_pitch_tolerance>20</app_balance_conf.startup_pitch_tolerance>
    <app_balance_conf.startup_roll_tolerance>8</app_balance_conf.startup_roll_tolerance>
    <app_balance_conf.startup_speed>30</app_balance_conf.startup_speed>
    <app_balance_conf.deadzone>0</app_balance_conf.deadzone>
    <app_balance_conf.current_boost>0</app_balance_conf.current_boost>
    <app_balance_conf.multi_esc>0</app_balance_conf.multi_esc>
    <app_balance_conf.yaw_kp>0</app_balance_conf.yaw_kp>
    <app_balance_conf.yaw_ki>0</app_balance_conf.yaw_ki>
    <app_balance_conf.yaw_kd>0</app_balance_conf.yaw_kd>
    <app_balance_conf.roll_steer_kp>0</app_balance_conf.roll_steer_kp>
    <app_balance_conf.brake_current>0</app_balance_conf.brake_current>
    <app_balance_conf.overspeed_delay>0</app_balance_conf.overspeed_delay>
    <app_balance_conf.fault_delay>0</app_balance_conf.fault_delay>
    <app_balance_conf.tiltback_constant>0</app_balance_conf.tiltback_constant>
    <app_balance_conf.roll_steer_erpm_kp>0</app_balance_conf.roll_steer_erpm_kp>
    <app_balance_conf.yaw_current_clamp>0</app_balance_conf.yaw_current_clamp>
    <app_balance_conf.adc_half_fault_erpm>1000</app_balance_conf.adc_half_fault_erpm>
    <app_balance_conf.setpoint_pitch_filter>0</app_balance_conf.setpoint_pitch_filter>
    <app_balance_conf.setpoint_target_filter>1</app_balance_conf.setpoint_target_filter>
    <app_balance_conf.setpoint_clamp>80</app_balance_conf.setpoint_clamp>
    <imu_conf.type>1</imu_conf.type>
    <imu_conf.mode>0</imu_conf.mode>
    <imu_conf.sample_rate_hz>200</imu_conf.sample_rate_hz>
    <imu_conf.accel_confidence_decay>1</imu_conf.accel_confidence_decay>
    <imu_conf.mahony_kp>0.3</imu_conf.mahony_kp>
    <imu_conf.mahony_ki>0</imu_conf.mahony_ki>
    <imu_conf.madgwick_beta>0.1</imu_conf.madgwick_beta>
    <imu_conf.rot_roll>0</imu_conf.rot_roll>
    <imu_conf.rot_pitch>0</imu_conf.rot_pitch>
    <imu_conf.rot_yaw>0</imu_conf.rot_yaw>
    <imu_conf.accel_offsets__0>0</imu_conf.accel_offsets__0>
    <imu_conf.accel_offsets__1>0</imu_conf.accel_offsets__1>
    <imu_conf.accel_offsets__2>0</imu_conf.accel_offsets__2>
    <imu_conf.gyro_offsets__0>0</imu_conf.gyro_offsets__0>
    <imu_conf.gyro_offsets__1>0</imu_conf.gyro_offsets__1>
    <imu_conf.gyro_offsets__2>0</imu_conf.gyro_offsets__2>
    <imu_conf.gyro_offset_comp_fact__0>0</imu_conf.gyro_offset_comp_fact__0>
    <imu_conf.gyro_offset_comp_fact__1>0</imu_conf.gyro_offset_comp_fact__1>
    <imu_conf.gyro_offset_comp_fact__2>0</imu_conf.gyro_offset_comp_fact__2>
    <imu_conf.gyro_offset_comp_clamp>5</imu_conf.gyro_offset_comp_clamp>
</APPConfiguration>

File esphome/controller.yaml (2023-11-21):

substitutions:
  device_name: "mixer"
  friendly_name: "Mixer"
  mqqt_root_topic: "testing"
  mqqt_retain_message: "false"

# ota:
#   safe_mode: true
#   password: !secret ota_password

esphome:
  name: ${device_name}
  friendly_name: ${device_friendly_name}

esp32:
  board: nodemcu-32s

logger:
  level: DEBUG
  baud_rate: 9600
  logs:
    canbus: INFO

wifi:
  networks:
  - ssid: !secret wifi_ssid_home
    password: !secret wifi_password_home
  - ssid: !secret wifi_ssid_makerspace
    password: !secret wifi_password_makerspace

# captive_portal:

mqtt:
  broker: "broker.lan"
  discovery_object_id_generator: device_name
  topic_prefix: ${mqqt_root_topic}/${device_name}

output:
  - platform: ledc
    pin: GPIO4
    id: motor_pwm_out
    frequency: 19531Hz

globals:
  - id: last_speed_sp_update_ms
    type: long
    initial_value: '0'
    restore_value: no

  - id: last_energy
    type: uint32_t
    restore_value: no
    initial_value: '0'

interval:      
  - interval: 200ms
    then:
      - lambda: |-
          // Update motor speed
          long current_ms = millis();
          
          float setpoint_next = id(speed_esp_percent).state;
          if (isnan(setpoint_next)) {
            setpoint_next = 0;
          }

          //int can_delta_ms = current_ms - id(last_speed_sp_update_ms);
          //if (can_delta_ms > 3000) {
          //  setpoint_next = 0;
          //}

          id(motor_pwm_out).set_level(setpoint_next / 100.0);

          if (setpoint_next > 0) {
            id(motor_fan_sw).turn_on();
            // ESP_LOGI("Received VESC actual speed: ", "%i", 1);
          } else {
            id(motor_fan_sw).turn_off();
            // ESP_LOGI("Received VESC actual speed: ", "%i", 0);
          }

sensor:
  - platform: template
    id: speed_esp_percent
    name: "speed_esp_percent"
    unit_of_measurement: "%"
    force_update: true
    internal: False
    state_topic: ${mqqt_root_topic}/${device_name}/mcu/speed_percentage/get
  - platform: template
    id: temperature_material
    name: "temperature_material"
    unit_of_measurement: "°C"
    force_update: true
    internal: False
    state_topic: ${mqqt_root_topic}/${device_name}/ds18b20_material/temperature/get
  - platform: template
    id: temperature_motor
    name: "temperature_motor"
    unit_of_measurement: "°C"
    force_update: true
    internal: False
    state_topic: ${mqqt_root_topic}/${device_name}/ds18b20_motor/temperature/get
  - platform: template
    id: speed_vesc_rpm
    name: "speed_vesc_rpm"
    unit_of_measurement: "RPM"
    force_update: true
    internal: False
    state_topic: ${mqqt_root_topic}/${device_name}/vesc/speed_motor/get
  - platform: pzemac
    current:
      name: "current"
      force_update: True
      state_topic: ${mqqt_root_topic}/${device_name}/pzem_016/current/get
    voltage:
      name: "voltage"
      force_update: True
      state_topic: ${mqqt_root_topic}/${device_name}/pzem_016/voltage/get
    energy:
      name: "energy"
      internal: True
      force_update: True
      on_value:
        - lambda: !lambda |-
            id(last_energy) = x;
    power:
      name: "power"
      force_update: True
      state_topic: ${mqqt_root_topic}/${device_name}/pzem_016/power/get
    frequency:
      name: "frequency"
      force_update: True
      state_topic: ${mqqt_root_topic}/${device_name}/pzem_016/frequency/get
    power_factor:
      name: "power_factor"
      force_update: True
      state_topic: ${mqqt_root_topic}/${device_name}/pzem_016/power_factor/get
    update_interval: 5s
  - platform: template
    name: "energy"
    id: energy_template
    update_interval: 60s
    force_update: True
    lambda: !lambda |-
      if (id(last_energy) > 0) { 
        return (id(last_energy));
      } else {
        return {};
      }  
    state_topic: ${mqqt_root_topic}/${device_name}/pzem_016/energy/get

switch:
  - platform: gpio
    id: motor_fan_sw
    pin: GPIO26
    internal: True


uart:
  rx_pin: GPIO19
  tx_pin: GPIO18
  baud_rate: 9600

modbus:
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

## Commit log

2023-08-14 Initial commit of the project
    [app.xml, controller.yaml, mixer-controller.kicad_pcb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]
2023-08-15 Added separate PCB for VESC ADC L-pass filter
    [vesc-adc-filter.kicad_pcb, vesc-adc-filter.kicad_sch]
2023-08-18 Added encoder breakout and updated other projects
    [encoder-breakout.kicad_pcb, encoder-breakout.kicad_sch, mixer-controller.kicad_pcb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]
2023-08-22 Final updates for manufacturing
    [bom.csv, designators.csv, encoder-breakout-panelized.kicad_pcb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]
2023-09-02 Changes after manufacting
    [controller.yaml, encoder-breakout.kicad_sch, mixer-interface.step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]
2023-11-21 Added PZEM and MQQT config
    [controller.yaml]
2024-01-19 Negative measured speed RPM values are replaces as zero in the interface
    [interface.yaml]
2024-01-19 Switched encoder places
